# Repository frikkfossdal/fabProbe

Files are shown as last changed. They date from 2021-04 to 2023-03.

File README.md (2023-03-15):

# Fab Touchprobe 

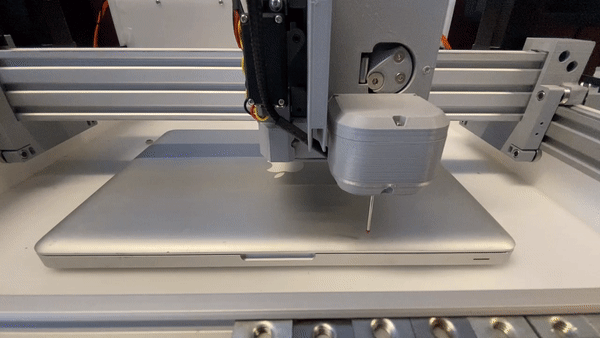
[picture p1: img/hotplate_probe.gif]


## What is it

A fabrication friendly design of a 3-DOF touch probe. At the heart of the design is a circuit board that lights up leds on probe contact. Probe is designed to be attached on [Jake Read's hotplate system](https://clank.tools/build/hotplate/index.html). 

## How to use it

The probe acts as a digital switch. Connect it to your favorite machine controller and start probing. 

**NB! First batch of circuits has wrong labeling on connector input. Ground and input voltage is switched. Study circuit before connecting and chech yourself!**

## How to make it

The repo contains all the files that are necassary to print the parts and make the circuit. There are currently two circuit designs: one that is pcb mill friendly (not tested!) and one circuit design meant for fabrication houses. I'm using the latter. Some notes: 

- Originally the probe uses [threaded steel-balls]() and dowels to form the kinematic mount but this could be modified to only use screws and dowels for easier sourcing.
- I print the probe casing with two different filaments, one transparent for making the circuit leds visible and one solid gray. If you rather print the casing as one solid merge the two casing bodies. 
- If you want to use a different probing stylus change the "nut diameter" of the nut on the *probe base* (see fusion model) to fit your chosen diameter. 

## BOM

| **Part Name** | **Description** | **Quantity** | **Link** |
|---|---|---|---|
| threaded steel ball | typically found in delta printers | 6 | [amazon](https://www.amazon.com/Bolsen-Threaded-Kossel-3D-Printer-Magnetic/dp/B07HQ72H1R) |
| steel dowels 5x10mm | | 3 | [mcmaster](https://www.mcmaster.com/93600a511/) |
| probe stylus m3x50  | | 1 | [ebay](https://www.ebay.com/itm/132811711640) |
| m4button x 8mm | | 6 | [mcmaster](https://www.mcmaster.com/93600a511/) |
| m3button x 14mm | | 3 | [mcmaster](https://www.mcmaster.com/92095A168/) |
| m3_locknut | | 3 | [mcmaster](https://www.mcmaster.com/90576A102/) |

## Develop notes 

- After discussing with Jake we agreed that the design of the probe needs to be modified with some way of offsetting the centering of the probe. Revision will follow in near future. 
- [Here](https://www.youtube.com/watch?v=ZvX3S8Ky3Ok) is a video showing how centering is done on a renishaw probe.
- [Instructable](https://www.instructables.com/CNC-Touch-Probe-Calibration/) on calibrating probe using gcode.
- Spring force matters. I have to do more testing to find good sensitivity.

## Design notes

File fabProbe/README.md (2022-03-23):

# Fab Touchprobe 

## What is it

A fabrication friendly design of a 3-DOF touch probe. At the heart of the design is a circuit board with a kinematic coupling where each contact point is wired in series. If the contact breaks the circuits output signal will go high. 

## How to use it
- more soon 

## How to make it

The repo contains all the files that are necassary to print the parts and make the circuit. There are currently two circuit designs: one that is pcb mill friendly and one that is meant for fabrication houses. I'm using the latter. 

# Log

## 2203_2022 

Starting logging quite late in the process. I'll add documentation of what I actually have done later but right now I'm focusing on debugging. I have a circuit and its not working. I'm suspecting that there is something wrong in the design around the NPN transistor. FOUND IT! The footprint of the transistor is flipped in terms of the transistor I actually bought. I hacked a quick solution by soldering the transistors to the circuit on their heads. What did we learn here: never blindly trust footprints that you find online and ALWAYS READ THE DATASHEET of the parts you are using. 

Let there be light.

I'll hopefully come back later this week and test the circuit on the duet. 

## Old log stuff - delete? 

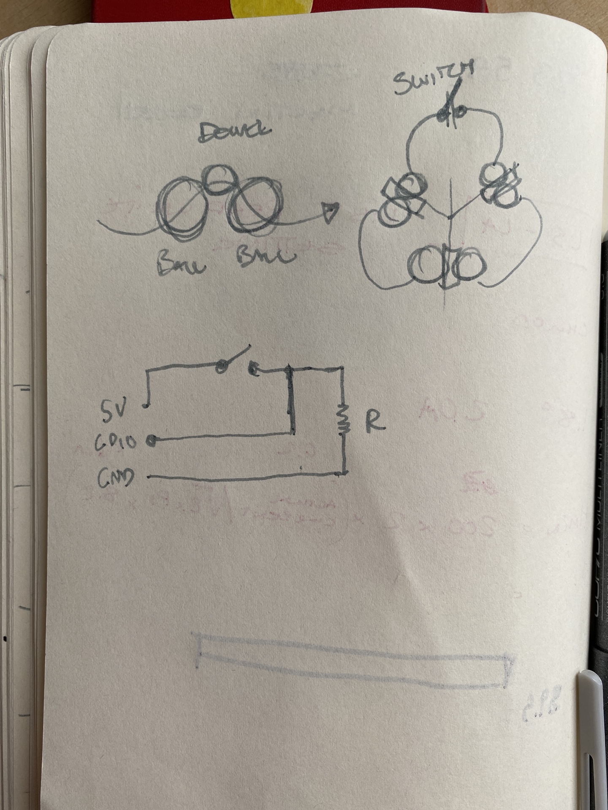
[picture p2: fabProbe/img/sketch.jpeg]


Here is a gif of the kinematic coupling priciple. The top-side is held in place by the magnets. If the probe touches something, the kinematic coupling will loose contact with one of the ball-couplings and break the circuit. 

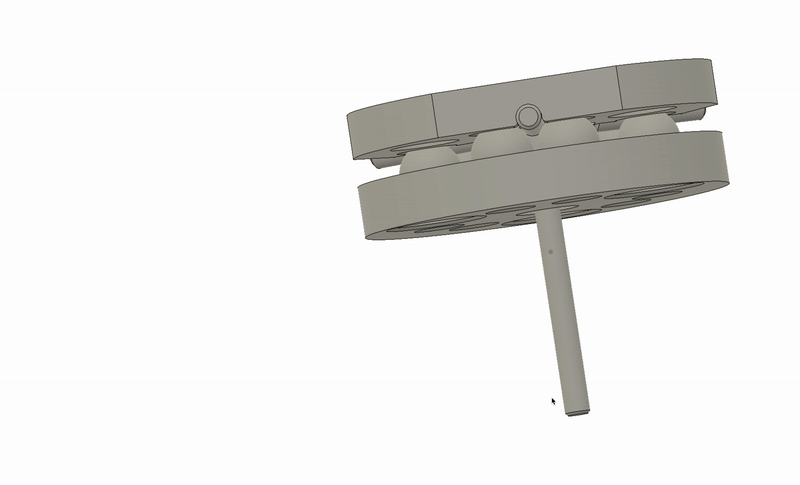
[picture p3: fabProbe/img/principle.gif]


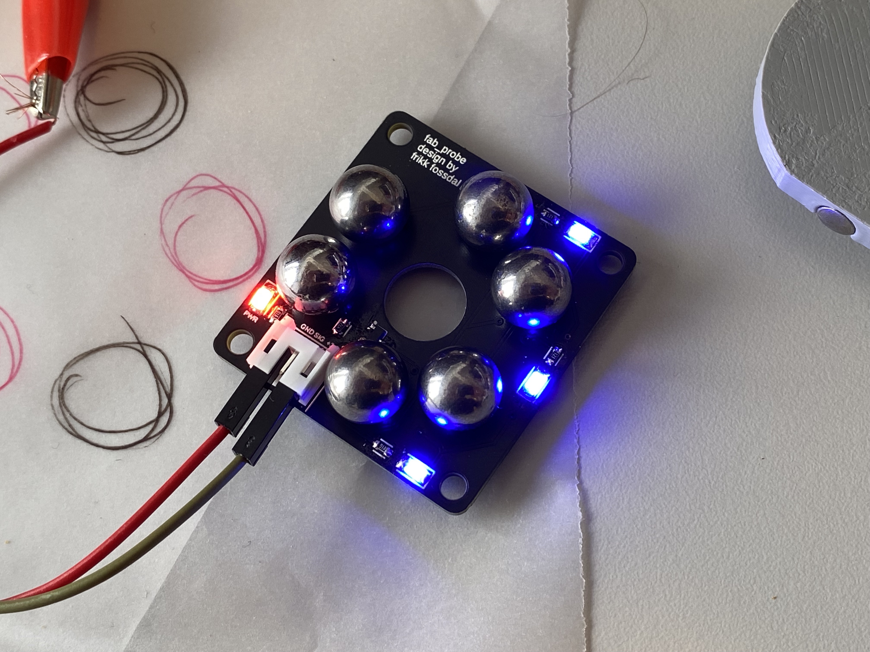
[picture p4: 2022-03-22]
img/probe_light.jpeg

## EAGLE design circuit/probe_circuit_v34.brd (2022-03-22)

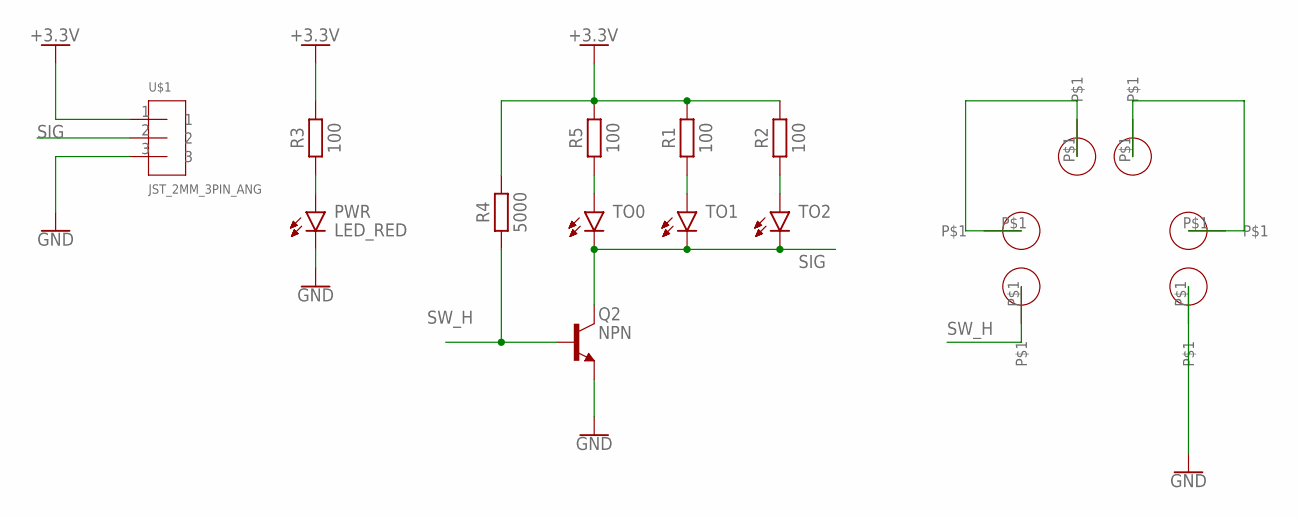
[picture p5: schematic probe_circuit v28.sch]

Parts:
F0, F1, F2, F3, F4, F5: 4MM_HOLE
PWR: LED_RED; LEDC3216X75N_FLAT-R
Q2: NPN; SOT95P237X112-3N
R1, R2, R3, R5: 100; RESC1608X60
R4: 5000; RESC1608X60
TO0, TO1, TO2: LED_BLUE; LEDC3216X75N_FLAT-B
U$1: JST_2MM_3PIN_ANG

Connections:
+3.3V: R1.2, R2.2, R3.2, R4.2, R5.2, U$1.1
GND: F5.P$1, PWR.C, Q2.2 (E), U$1.3
unnamed: PWR.A, R3.1
unnamed: F1.P$1, F2.P$1
unnamed: R5.1, TO0.A
unnamed: F3.P$1, F4.P$1
unnamed: R1.1, TO1.A
unnamed: R2.1, TO2.A
SIG: Q2.3 (C), TO0.C, TO1.C, TO2.C, U$1.2
SW_H: F0.P$1, Q2.1 (B), R4.1

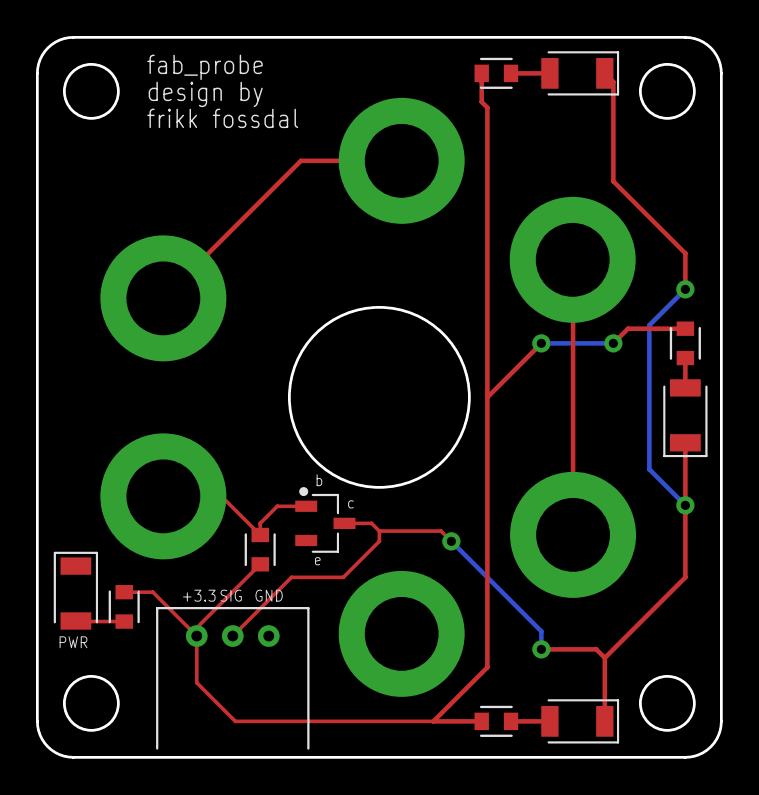
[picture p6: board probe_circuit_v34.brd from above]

Board: 2 copper layers, 38.0 x 40.0 mm, 17 parts (0 on the bottom side), 10 nets.

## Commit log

2021-04-08 switching to mobile
2022-03-22 documentation first round of circuit
2022-03-22 added circuit files
    these are updated with transistor fix and text fix after debugging version 1
    [probe_circuit v34.brd, probe_circuit_v27.sch]
2022-03-23 Create probe_circuit v30.step
2022-05-04 new project folder
    [probe_circuit v34.brd, probe_circuit_v27.sch]
2022-05-18 updated files
    [probe_circuit v28.sch, probe_circuit v34.brd, probe_circuit_v27.sch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]

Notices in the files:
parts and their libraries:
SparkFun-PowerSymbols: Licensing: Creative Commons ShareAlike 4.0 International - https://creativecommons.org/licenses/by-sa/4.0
